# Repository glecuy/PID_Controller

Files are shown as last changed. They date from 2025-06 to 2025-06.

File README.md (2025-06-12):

## Universal motor PID speed regulator for bench drill.

ATMEGA 328 based DC motor electronic regulator.

It uses pms67/PID library (https://github.com/pms67/PID)

# Hardware design
  - A potentiometer is used at input to select desired speed.
  - Actual speed is measured and sent to controller
  - ATmega microcontroller compute resulting PWM signal
  - A MOSFET modulates MOTOR DC voltage.
  - Switching frequency is 32KHz.

# Software design
  - Potentiometer position is read via ADC3 (setpoint)
  - Speed sensor connected to INT0 and measured by counting timer2 ticks (measurement)
  - Sampling rate is set to 0.1 Sec and call to PIDController_Update()
  - Output is used to control motor voltage (PWM)
  - Calculations are done in floating point and normalized to one.

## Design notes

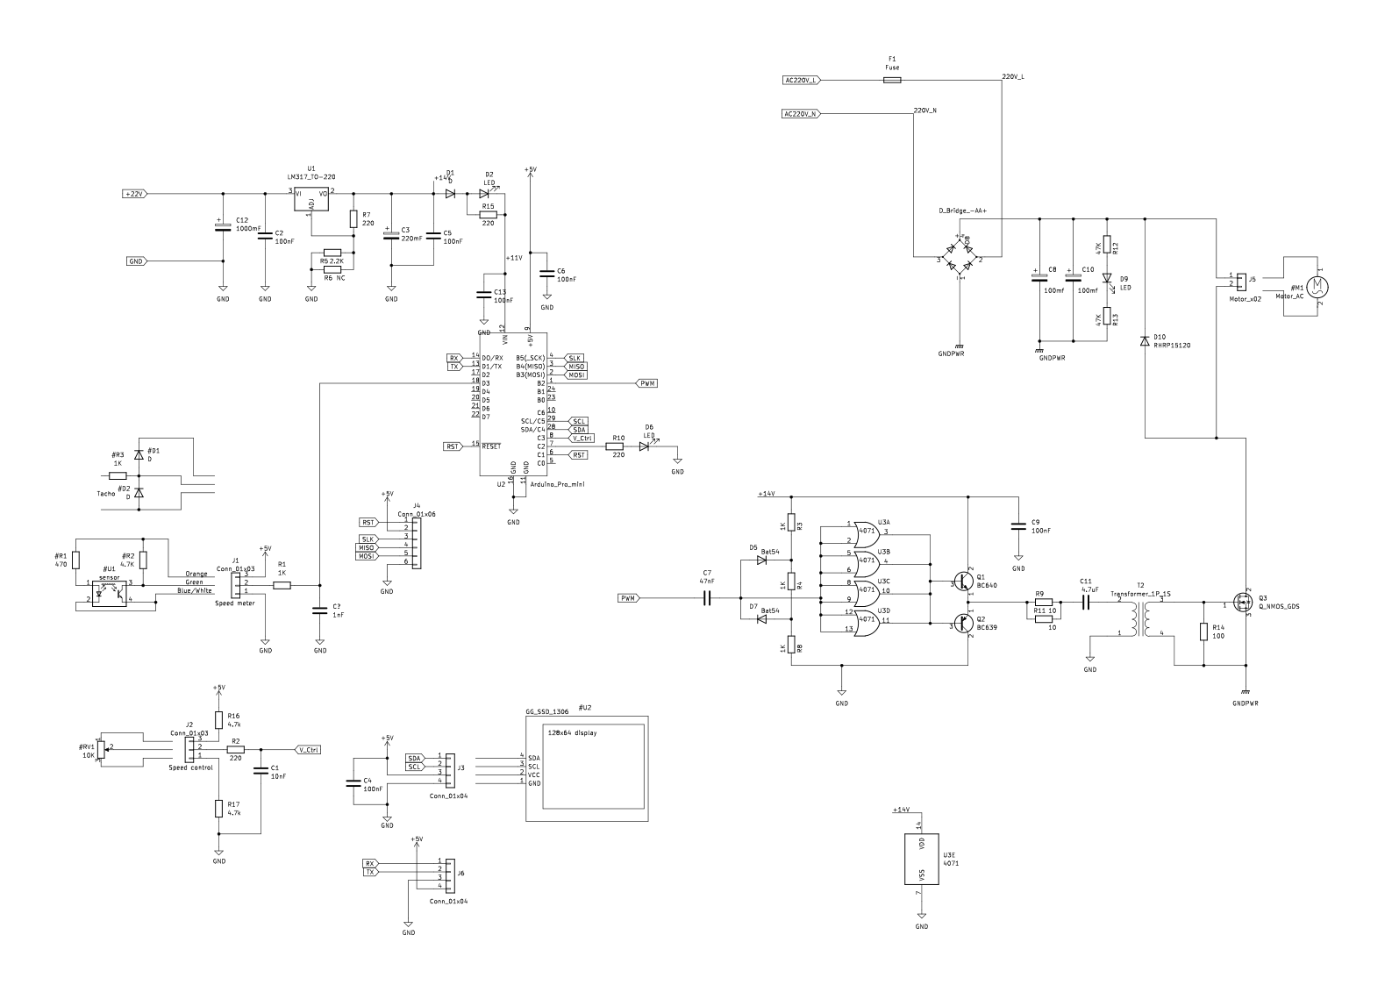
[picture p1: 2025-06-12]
PidControllerSch.png

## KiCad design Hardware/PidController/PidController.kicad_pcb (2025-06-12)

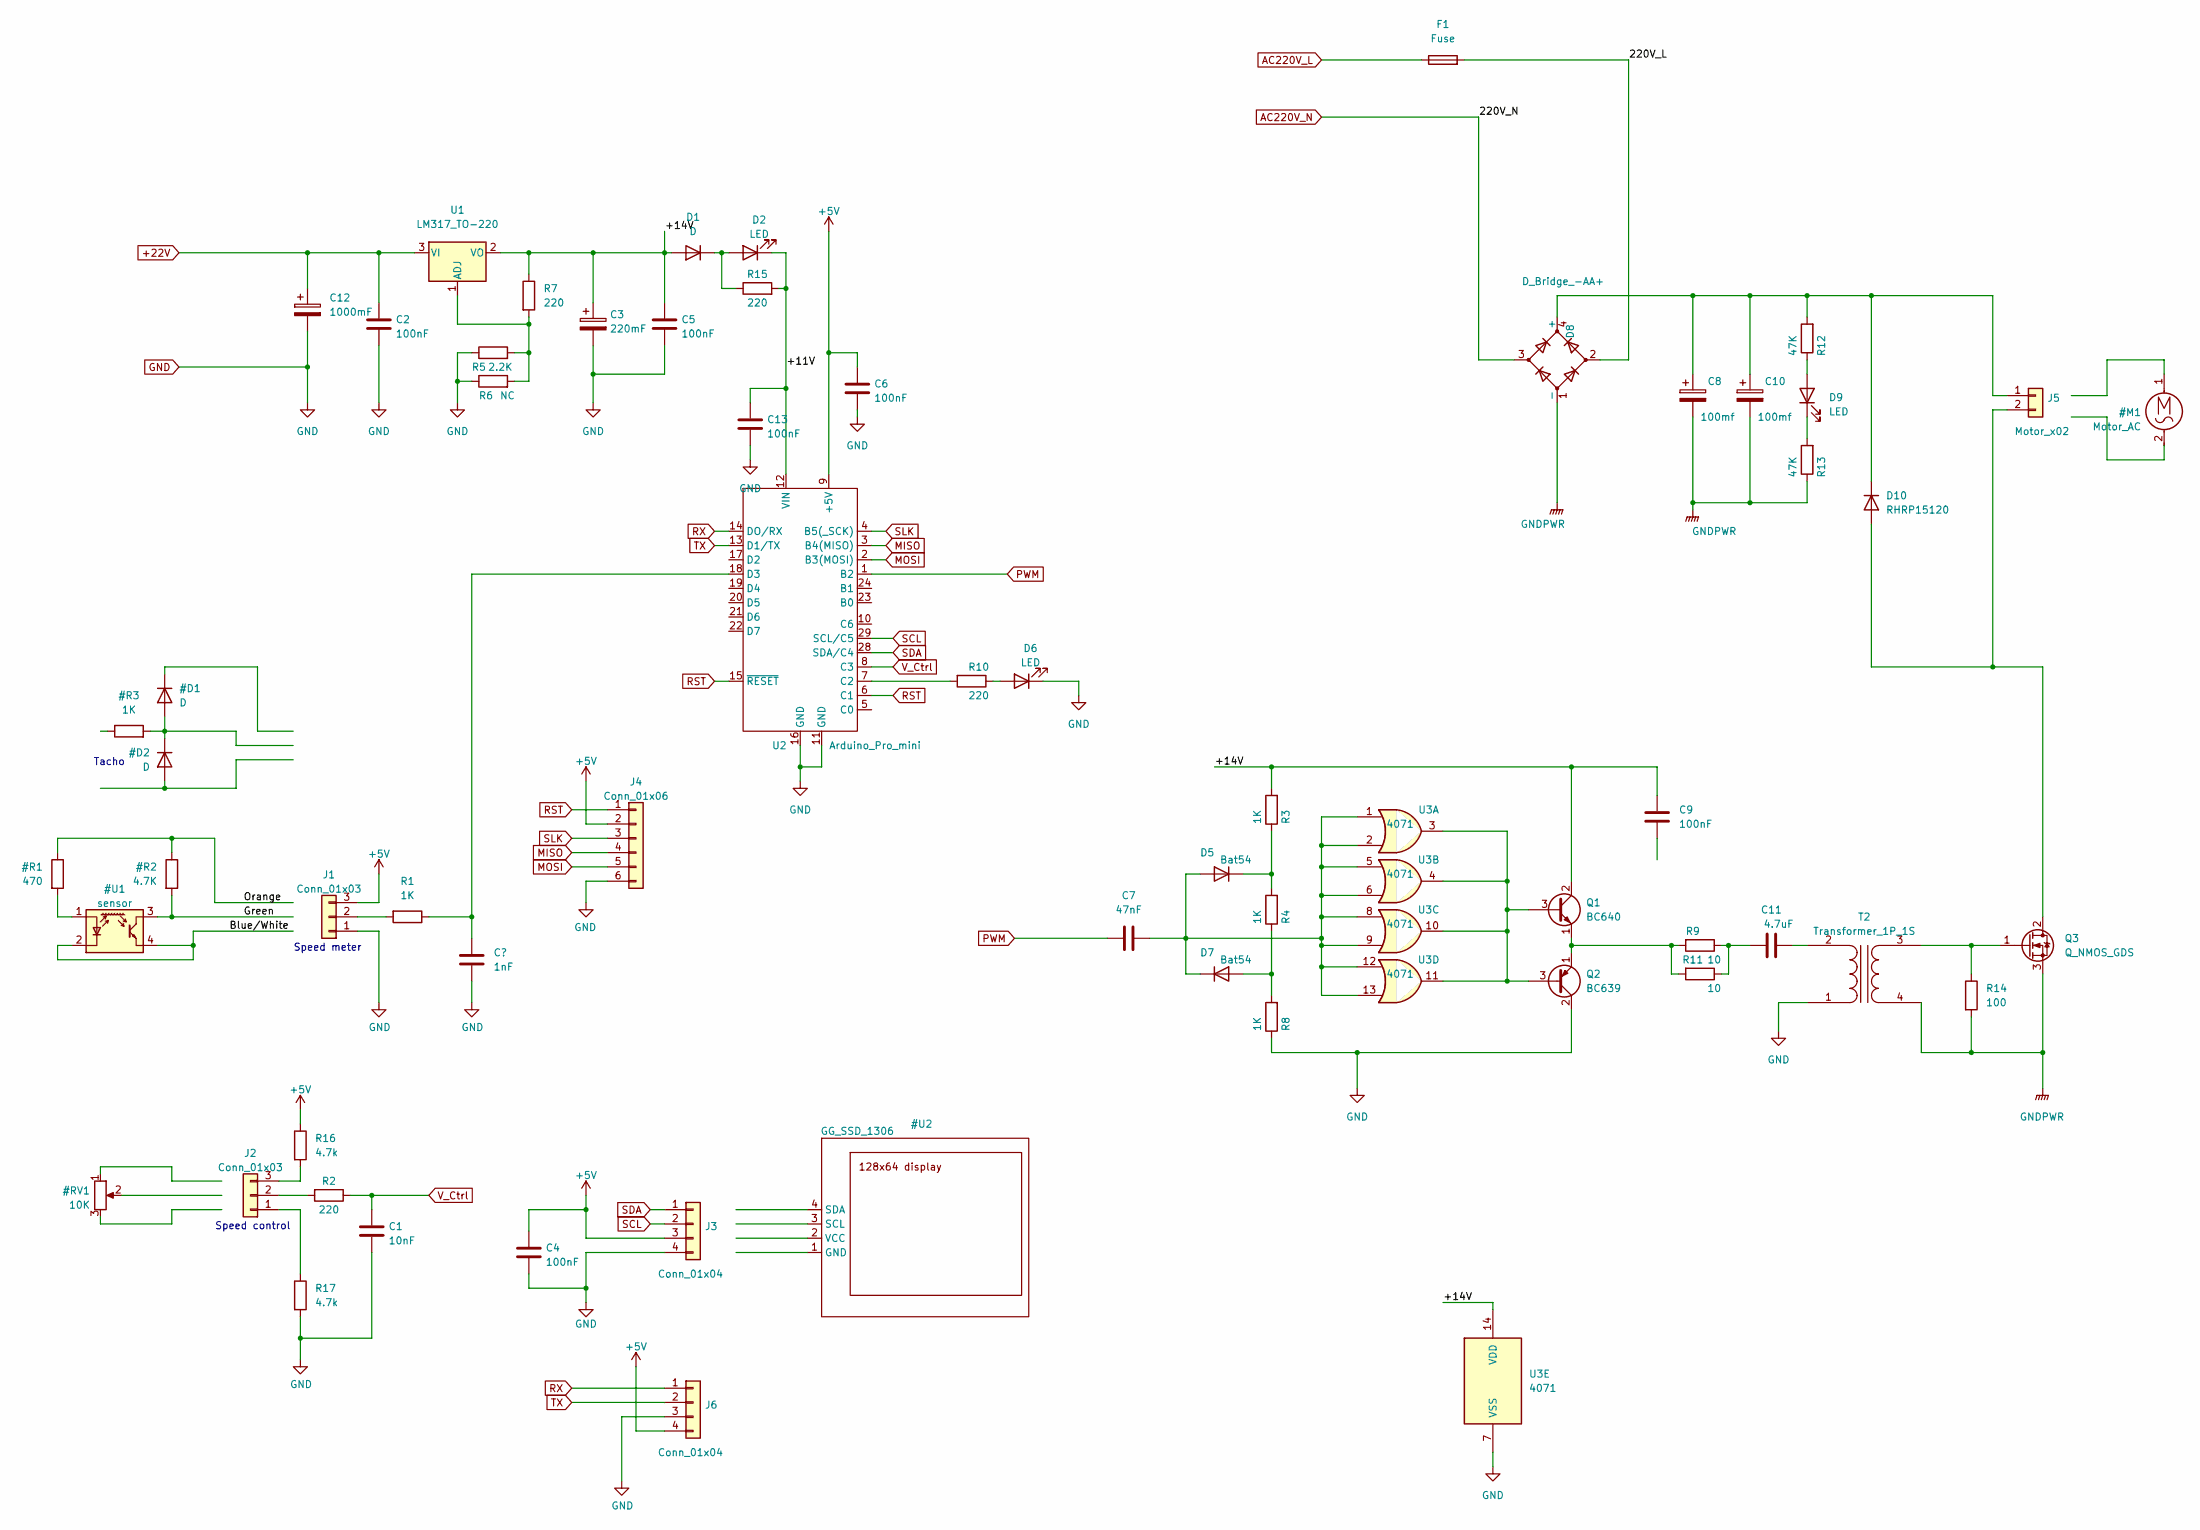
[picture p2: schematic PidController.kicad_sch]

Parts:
C1: 10nF; C_0805_2012Metric_Pad1.18x1.45mm_HandSolder
C2, C5: 100nF; LED_1210_3225Metric
C3: 220mF; CP_Radial_D8.0mm_P5.00mm
C4, C6, C9, C13: 100nF; C_0805_2012Metric_Pad1.18x1.45mm_HandSolder
C7: 47nF; C_0805_2012Metric_Pad1.18x1.45mm_HandSolder
C8, C10: 100mf; CP_Radial_D18.0mm_P7.50mm
C11: 4.7uF; C_Film_5.08
C12: 1000mF; CP_Radial_D8.0mm_P5.00mm
D1: D; D_5KPW_P12.70mm_Horizontal
D2, D6: LED; LED_2010_5025Metric
D5, D7: Bat54; D_SOT-23_ANK
D8: D_Bridge_-AA+; Diode_Bridge_300V
D9: LED; LED_1210_3225Metric_Pad1.42x2.65mm_HandSolder
D10: RHRP15120; D_TO-220-2_Vertical
F1: Fuse; Fuse_5X20
J1: Conn_01x03; GG_PinHeader_1x03
J2: Conn_01x03; JWT_1x03_P3.96mm_Vertical
J3, J6: Conn_01x04; GG_PinHeader_1x04
J4: Conn_01x06; GG_PinHeader_1x06
J5: Motor_x02; MotorConnector_2
Q1: BC640; TO-92_delta
Q2: BC639; TO-92_delta
Q3: Q_NMOS_GDS; TO-247-3_Vertical
R1, R3, R4, R8: 1K; R_1206_3216Metric_Pad1.30x1.75mm_HandSolder
R2, R7, R10, R15: 220; R_1206_3216Metric_Pad1.30x1.75mm_HandSolder
R5: 2.2K; R_1206_3216Metric_Pad1.30x1.75mm_HandSolder
R6: NC; R_1206_3216Metric_Pad1.30x1.75mm_HandSolder
R9, R11: 10; R_1206_3216Metric_Pad1.30x1.75mm_HandSolder
R12, R13: 47K; R_1206_3216Metric_Pad1.30x1.75mm_HandSolder
R14: 100; R_Axial_DIN0309_L9.0mm_D3.2mm_P12.70mm_Horizontal
R16, R17: 4.7k; R_1206_3216Metric_Pad1.30x1.75mm_HandSolder
T2: Transformer_1P_1S; Transformer_Toroid_Horizontal_D18.0mm
U1: LM317_TO-220; TO-263-2
U2: Arduino_Pro_mini; GG_Arduino_Pro_MiniEVB
U3: 4071; DIP-14_W8.89mm_SMDSocket_LongPads

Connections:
+5V: C4.1, C6.1, J1.3, J3.3, J4.2, J6.4, R16.1, U2.9 (+5V)
+22V: C2.1, C12.1, U1.3 (VI)
/220V_L: D8.2, F1.2
/+11V: C13.1, D2.1 (K), R15.2, U2.12 (VIN)
/+14V: C3.1, C5.1, C9.2, D1.2 (A), Q1.2 (C), R3.2, R7.1, U1.2 (VO), U3.14 (VDD)
AC220V_L: F1.1
AC220V_N: D8.3
GND: C1.2, C2.2, C3.2, C4.2, C5.2, C6.2, C12.2, C13.2, D6.1 (K), J1.1, J3.4, J4.6, J6.3, Q2.2 (C), R5.1, R6.1, R8.1, R17.2, T2.1 (AA), U2.11 (GND), U2.16 (GND), U3.7 (VSS)
GNDPWR: C8.2, C10.2, D8.1 (-), Q3.3 (S), R13.1, R14.2, T2.4 (SB)
MISO: J4.4, U2.3 (B4(MISO))
MOSI: J4.5, U2.2 (B3(MOSI))
unnamed: C7.2, D5.2 (A), D7.1 (K), U3.1, U3.2, U3.5, U3.6, U3.8, U3.9, U3.12, U3.13
unnamed: C8.1, C10.1, D8.4 (+), D10.1 (K), J5.1, R12.2
unnamed: C11.1, R9.1, R11.1
unnamed: C11.2, T2.2 (AB)
unnamed: D1.1 (K), D2.2 (A), R15.1
unnamed: D5.1 (K), R3.1, R4.2
unnamed: D6.2 (A), R10.1
unnamed: D7.2 (A), R4.1, R8.2
unnamed: D9.1 (K), R13.2
unnamed: D9.2 (A), R12.1
unnamed: D10.2 (A), J5.2, Q3.2 (D)
unnamed: J1.2, R1.2
unnamed: J2.1, R17.1
unnamed: J2.2, R2.2
unnamed: J2.3, R16.2
unnamed: Q1.1 (E), Q2.1 (E), R9.2, R11.2
unnamed: Q1.3 (B), Q2.3 (B), U3.3, U3.4, U3.10, U3.11
unnamed: Q3.1 (G), R14.1, T2.3 (SA)
unnamed: R1.1, U2.18 (D3)
unnamed: R5.2, R6.2, R7.2, U1.1 (ADJ)
unnamed: R10.2, U2.7 (C2)
PWM: C7.1, U2.1 (B2)
RST: J4.1, U2.6 (C1), U2.15 (~RESET)
RX: J6.1, U2.14 (DO/RX)
SCL: J3.2, U2.29 (SCL/C5)
SDA: J3.1, U2.28 (SDA/C4)
SLK: J4.3, U2.4 (B5(_SCK))
TX: J6.2, U2.13 (D1/TX)
V_Ctrl: C1.1, R2.1, U2.8 (C3)

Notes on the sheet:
Tacho
Speed control
Speed meter

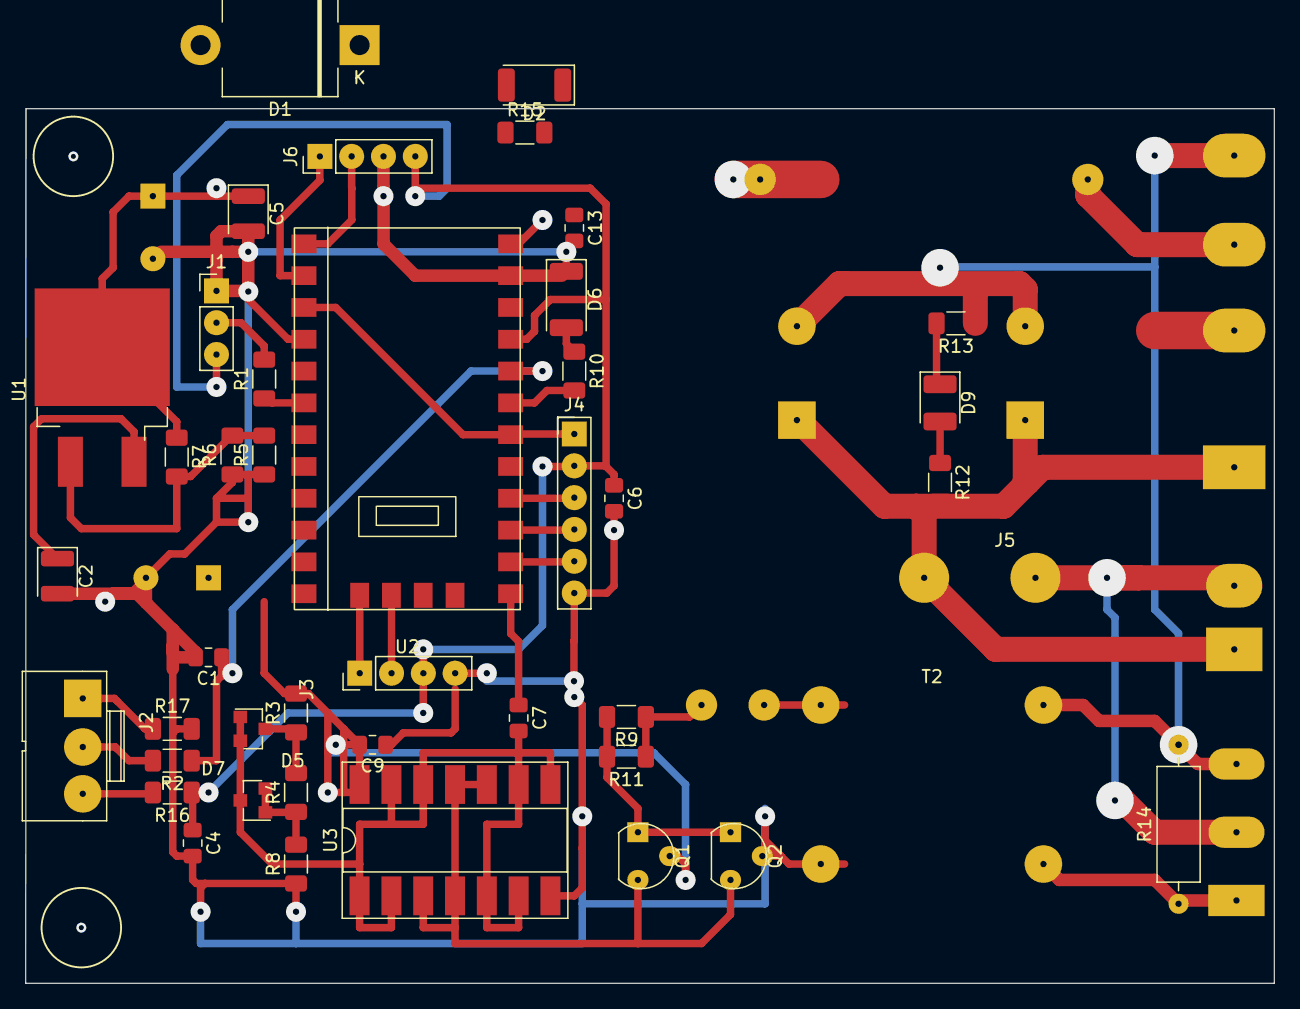
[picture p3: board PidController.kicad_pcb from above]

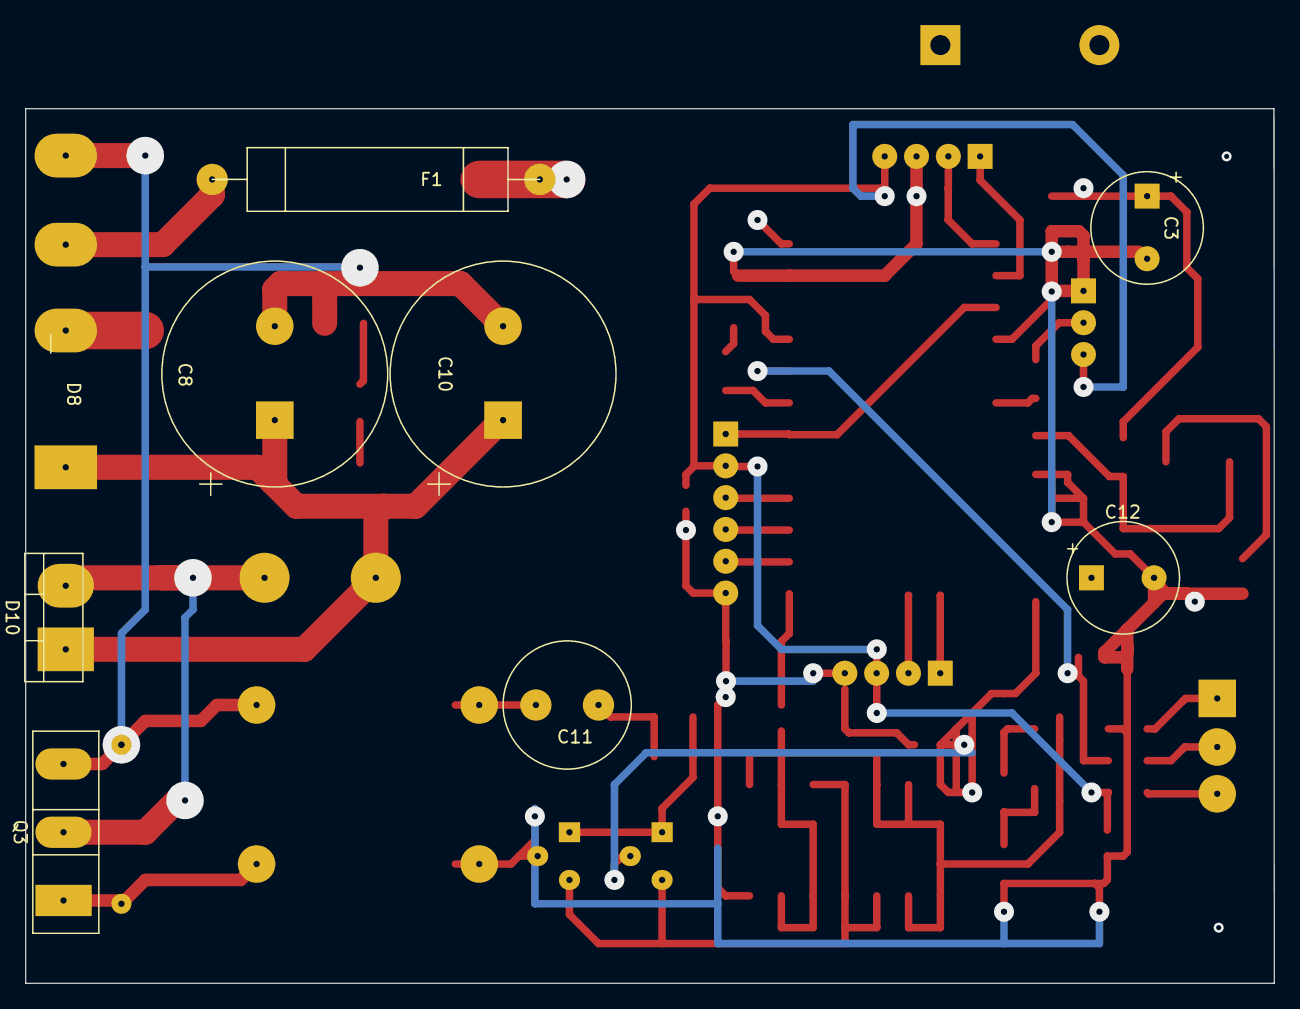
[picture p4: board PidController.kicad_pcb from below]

Board: 2 copper layers, 99.7 x 69.8 mm, 52 parts (9 on the bottom side), 38 nets.

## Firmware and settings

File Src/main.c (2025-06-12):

/*****************************************************************************
*
*
*  File Name    : main.c
*  Version      : 1.0
*
*****************************************************************************/
#include <avr/io.h>
#include <string.h>
#include <stdio.h>
#include <util/delay.h>
#include <avr/interrupt.h>
#include <avr/pgmspace.h>
#include <avr/eeprom.h>

#include <avr/sleep.h>
#include <avr/wdt.h>

#include "uart_printf.h"
#include "timer0.h"
#include "ssd1306.h"
#include "analogIn.h"

#include "PID.h"
#include "debug.h"

// On board LED (Pro Mini board)
#define LED1        PINB5

// On main board LED
#define LED2        PINC2


// PWM  -  Output Compare Match B Output
#define PWM_OUTPUT  PINB2



#define SoftReset() wdt_enable(WDTO_30MS); while(1) {}


uint8_t dbg_var;

/* Global variables */
static char TempString[16];  // Dangerous !

static volatile uint16_t zc_count;
static volatile uint16_t zc_width;

static volatile uint8_t  cnt2H;

static volatile uint32_t T2_ticks_count = 0UL;

static volatile uint16_t _meas_count;

#define LED1_OFF()      (PORTB &= ~(1 << PINB5))
#define LED1_ON()       (PORTB |= (1 << PINB5))
#define LED1_TOGGLE()   { if ( PORTB & (1 << PINB5) ) LED1_OFF(); else LED1_ON(); }


#define LED2_OFF()      (PORTC &= ~(1 << PINC2))
#define LED2_ON()       (PORTC |= (1 << PINC2))
#define LED2_TOGGLE()   { if ( PORTC & (1 << PINC2) ) LED2_OFF(); else LED2_ON(); }



#define Tacho_Interrupt_disable() EIMSK &= ~(1 << INT0)
#define Tacho_Interrupt_enable()  EIMSK |= (1 << INT0)

/* Initialise PID controller
 * Most values come from PID_Test.c */
//static PIDController PID_Controller = {
//                .Kp=2.0f, .Ki=0.5f, .Kd=0.25f,
//                .tau=0.02f,
//                .limMin=-1.0f, .limMax=+1.0f,
//                .limMinInt=-5.0f, .limMaxInt=+5.0f,
//                .T=(TIMER_TICK_MS/1000.0f)
//};

static PIDController PID_Controller = {
        .Kp=0.4f,.Ki=1.0f,.Kd=0.02f,
        .tau=0.005f,
        .limMin=0.0f, .limMax=+1.0f,
        .limMinInt=0.0f, .limMaxInt=+5.0f,
        .T=0.100f
};


/* Tacho metter is connected to INT0 pin
 * (Was INT1 before HW failure !)
 * 4 interrupts expected for one revolution */
ISR(INT0_vect)
{
    uint16_t count;
    // Read HW timer
    count  = TCNT2;
    // Read SW counter
    count |= (cnt2H<<8);

    // Reset timer
    TCNT2 = 0;
    cnt2H = 0;

    _meas_count++;
    T2_ticks_count += (uint32_t)count;

    LED2_TOGGLE();
}

/* Timer 2overflow interrupt
 * Allows ticks count beyond 255 */
ISR(TIMER2_OVF_vect)
{
    // Count overflows (15..8 bits)
    if ( cnt2H < 255 )
        cnt2H++;
}


void io_ports_init( void ){
    DDRB = 0;
    DDRB |= (1 << LED1);    // Set LED as output

    DDRC = 0;
    DDRC |= (1 << LED2);     // Set LED as output
    // Keep PINC1    as Input (Connected to reset)

    DDRC |= (1 << DBG_PIN);     // Debug


    DDRB |= (1 << PWM_OUTPUT);  // Set PWM signal output for MOSFET gate drive

    // Gate signal OFF
    PORTB &= ~(1<<PWM_OUTPUT);

}



/* INT0 */
void Tacho_Interrupt_init(void){

    EICRA &= ~((1<<ISC01) | (1<<ISC00));
    EICRA |= (1<<ISC01) | (1<<ISC00);   // The rising edge of INT0 generates an interrupt request.

    //EICRA |= (0<<ISC01) | (1<<ISC00);   // Any logical change on INT0 generates an interrupt request.

    EIMSK |= (1 << INT0);  // PIN D2 (INT0)

}


void ClockSetup(void){
/*
The CAL[6:0] bits are used to tune the frequency within the selected range.
  A setting of 0x00 gives the
lowest frequency in that range and a setting of 0x7F gives the highest frequency in the range.
*/

    // Value to fix fake chineese ATMEGA328 :
    //OSCCAL = 0x80 | 0x4F;
}




/* Timer 1 is used to generate PWM output signal
 *
 *
 ***************************************************************/
void timer1Setup(void){

    // Set up Timer1
    // Fast PWM - non-inverting - mode PWM - 8 bit
    TCCR1A = (1 << COM1B1) | (0 << COM1B0) | (0 << WGM11) | (1 << WGM10);

    // Fast PWM - 8 bit - mode 7
    TCCR1B = (0 << WGM13) | (1 << WGM12);

    // CS[2:0] Prescaler setting
    // 001 clk/1
    // 010 clk/8
    // 011 clk/64
    // 100 clk/256
    // 101 clk/1024
    TCCR1B |= ((0 << CS12) | (0 << CS11) | (1 << CS10));
}

void set_PWM_Value( uint16_t pwm ){
    OCR1B = pwm;

}

/* Timer 2 is used for Tachometer
 * Frequency is measured by determining period length
 * of the tachometer signal
 *
 ***************************************************************/
void timer2Setup(void){
    // Set up Timer2
    TCNT2 = 0;      //set timer to zero, may not be necessary
    TCCR2A = 0;     //normal counting up - output compare pins not used, initially zero so not necessary

    // Start timer at Fcpu/1024
    // F = 8000000/1024 = 7812.5
    // t = 1024/8000000 = 0.000128 (Sec)

    // Tin =  CNT * t
    // Fin = 1 / (CNT * t)
    // Fin = 1 / ((CNT * 1024) / 8000000)
    // Fin = 8000000 / (CNT * 1024)
    // 256 -> RPM Min = 919 , 1024 > RPM Min = 229
    //TCCR2B |= ((1 << CS22) | (1 << CS21) | (0 << CS20));

    // 64
    TCCR2B |= ((1 << CS22) | (0 << CS21) | (0 << CS20));

    // 32
    //TCCR2B |= ((0 << CS22) | (1 << CS21) | (1 << CS20));

    // 8
    //TCCR2B |= ((0 << CS22) | (1 << CS21) | (0 << CS20));

    // Enable overflow interrupt
    TIMSK2 = 1<<TOIE2;

}


uint8_t db_on;


void print_uint_as_fixed_point( int digits, int pos, uint32_t n ){
    char text[32];
    int i;
    uint32_t num = n;
    int d;
    char *ptr;

    for ( i=digits-1 ; i>=0 ; i-- ){
        d = num %10;
        num /= 10;
        text[i] = '0' + d;
        if ( i==pos ){
            i--;
            text[i] = '.';
        }
    }
    text[digits]=' ';
    text[digits+1]='\0';
    ptr = text;
    while ( *ptr ){
        putchar( *ptr );
        ptr++;
    }

}

/*
 * Replace printf %f for AVR microcontroleur
 *  output format used for python plot tool
 */

void DoAvrPrint( uint32_t t, float setpoint, float measurement, float out ){

    print_uint_as_fixed_point( 6, 3, t);
    print_uint_as_fixed_point( 6, 2, (uint32_t)(setpoint*10001) );
    print_uint_as_fixed_point( 6, 2, (uint32_t)(measurement*10001) );
    print_uint_as_fixed_point( 8, 2, (uint32_t)(out*1000001) );

    putchar( '\n');
}


uint32_t GetRpmOrderInput(void){
    uint32_t rpm;
    uint32_t Vin=0;

    Vin = (uint32_t)valVCtrl();

    rpm = (( 1000 * Vin ) / 255 );

    // Return rpm in parts per thousand.
    return rpm;
}


#define MAX_RPM     6000.
#define MIN_RPM     800
#define RPM_RAMP_UP 200
#define SPIN_UP     10

int main(void)
{
    unsigned long Tick100ms=0;

    uint32_t SetRPM=0;
    uint32_t RampUpRPM=0;
    int SpinUpCnt=0;


    uint16_t pwmValue;

    uint32_t CNT;
    uint16_t MeasCount;

    uint16_t loopCtrl=0;

    float RPM;

    // Turn all pullup restistors ON
    PORTB = 0xFF;
    PORTC = 0xFF;
    PORTD = 0xFF;

    io_ports_init();
    LED1_ON();

    ClockSetup();
    timer0_init();

    AnalogInInit();

    //ssd1306_init();

    Tacho_Interrupt_init();

    timer1Setup();

    timer2Setup();

    PIDController_Init(&PID_Controller);

    //  Enable global interrupts
    sei();

    // Initialize UART print
    uart_printf_init();

    printf("Hello AVR\n\n");

    LED1_OFF();

    RampUpRPM = MIN_RPM;
    while( 1 ){
        if ( timer0_Get100msTicks() != Tick100ms )
        {
            Tick100ms = timer0_Get100msTicks();
            //LED1_TOGGLE();
            DBGPIN_TOGGLE();


            SetRPM = GetRpmOrderInput();
            SetRPM = SetRPM * (MAX_RPM-MIN_RPM)/1000 + MIN_RPM;

            if ( SetRPM > RampUpRPM ){
                SetRPM = RampUpRPM;
                RampUpRPM += RPM_RAMP_UP;
            }
            //printf("SetRPM=%lu\n", SetRPM );

            //uint32_t CNT = (uint32_t)_tacho_count;
            // Critical section
            Tacho_Interrupt_disable();
                CNT = T2_ticks_count;
                T2_ticks_count=0;
                MeasCount = _meas_count;
                _meas_count=0;
            Tacho_Interrupt_enable();

            /* RPM = (60 * f) / 4 ;  4 pulses per revolution */
            /* div32 prescaler) */
            if ( MeasCount > 0 ){
                RPM = (float)((8000000.0*60.0 / (CNT * 64))/4.0) * (float)MeasCount;
            }
            else{
                // Let some cycles to machine to start
                if ( SpinUpCnt < SPIN_UP ){
                    SpinUpCnt++;
                }else{
                    SpinUpCnt = 0;
                }
                RPM = 0;
            }

            if ( ( RPM == 0 ) && ( SpinUpCnt >= SPIN_UP ) ){
                RampUpRPM = MIN_RPM;
                PIDController_Init(&PID_Controller);
            }


            /* Compute new control signal */
            PIDController_Update(&PID_Controller, ((float)SetRPM)/MAX_RPM, RPM/MAX_RPM  );
            DoAvrPrint( (Tick100ms & 0xFF)*100, ((float)SetRPM)/MAX_RPM, RPM/MAX_RPM, PID_Controller.out );

            pwmValue = (uint16_t)(uint32_t)(PID_Controller.out*100.0);
            if ( pwmValue > 64){
                pwmValue = 64;
            }
            if ( pwmValue < 2){
                pwmValue = 2;
            }

            set_PWM_Value( pwmValue );

            if ( ++loopCtrl % 10 == 0 ){
                //uint32_t uSetRPM = SetRPM;

                //printf("pid.out=%lu\n", (uint32_t)(PID_Controller.out*100.0) );
                //printf("SetRPM=%lu RPM=%lu OUT=%u\n", uSetRPM, (uint32_t)RPM, pwmValue);
                //printf("SetRPM=%u VCTRL=%u\n", SetRPM, valVCtrl() );
                //printf("CNT = %lu  RPM=%lu (%u)\n", CNT, (uint32_t)(RPM+0.5), MeasCount );
                //printf("CNT = %lu  cnt=%lu (%u)\n", CNT, CNT/MeasCount, MeasCount );
            }

        }
    }


  return 0;
}


/* EOF  */

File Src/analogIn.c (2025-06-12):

/*
    analogIn.c

    Temperature capture
    combustion detection


 */

#include <avr/io.h>
#include <string.h>
#include <stdio.h>
#include <util/delay.h>
#include <avr/interrupt.h>

volatile unsigned short VCtrlVal;


void AnalogInInit( void )
{
    ADMUX  = 0x3;  // 0011 use ADC3

    //ADMUX |= (1 << REFS1) | (1 << REFS0);  // use 1.1V as the reference
    ADMUX |= (0 << REFS1) | (1 << REFS0);    // AVCC with external capacitor at AREF pin
    //ADMUX |= (1 << ADLAR);                 // Right adjust for 8 bit resolution
    ADMUX &= ~(1 << ADLAR);                  // clear for 10 bit resolution

    ADCSRA  = (1 << ADPS2) | (1 << ADPS1) | (1 << ADPS0); // 128 prescale for 16Mhz
    //ADCSRA |= (1 << ADATE);   // Set ADC Auto Trigger Enable

    ADCSRB = 0;               // 0 for free running mode

    ADCSRA |= (1 << ADEN);    // Enable the ADC
    ADCSRA |= (1 << ADIE);    // Enable Interrupts

    ADCSRA |= (1 << ADSC);    // Start the ADC conversion
}



ISR(ADC_vect)
{

    VCtrlVal  =  (unsigned short)ADCL;
    VCtrlVal |= (ADCH << 8);     // ADCH is read so ADC can be updated again

    ADCSRA |= (1 << ADSC);    // Re-start the ADC conversion
}

/*
 * Returns VCtrl
 *
 *****************************************/
unsigned short valVCtrl( void )
{
    return (255 - VCtrlVal / 4) & 0xFF;
}


#if 0 //Dual input
ISR(ADC_vect)
{

    if ( MuxValue == 0x06 ){
        FlameVal  =  (unsigned short)ADCL;
        FlameVal |= (ADCH << 8);     // ADCH is read so ADC can be updated again
        MuxValue = 0x07;
        //MuxValue = 0x08;   // Internal temp
    }
    else {
        TemperatureVal  =  (unsigned short)ADCL;
        TemperatureVal |= (ADCH << 8);     // ADCH is read so ADC can be updated again
        MuxValue = 0x06;
    }

    ADMUX &= ~0x0F;           // Clear MUX[3..0]
    ADMUX |=  MuxValue;       // Change value
    ADCSRA |= (1 << ADSC);    // Re-start the ADC conversion
}
#endif

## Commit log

2025-06-12 Initial commit, Triac control tested
    [PidController.kicad_pcb, PidController.kicad_sch]
2025-06-12 Add motor simulator
2025-06-12 Integrate PID code from pms67/PID package
2025-06-12 First tests done, first PID params tuning
    [PidController.kicad_pcb, PidController.kicad_sch]
2025-06-12 Improve PID parameters with bench drill
    [PidController.kicad_sch]
